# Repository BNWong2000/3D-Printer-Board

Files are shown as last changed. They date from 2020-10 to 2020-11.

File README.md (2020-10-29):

# 3D-Printer-Board
A custom, 3D printer controller, intended to run Klipper. All pcb source files were made in kiCAD. This project utilizes the stock kiCAD library for basic components (Resistors, Capacitors, Diodes, Inductors, Connectors, etc), and for the main chip (STM32F407IGT6). All other components were made as a custom library. 

#### Features:
* STM32F407IGT6 32 bit MCU
* 9 Silent Stepper Drivers (Trinamic TMC 2209 with UART control)
* 8 Fan output FETs
   * Selectable Voltage for each fan using jumpers. (24V, 12V or 5v)
* 8 Heater output FETs (including 1 high power FET for heated beds and 1 high power FET for heated chamber)
* High power step down converter to 5v (max 5A)
   * This is enough to power the raspberry pi (which only needs 3A at 5v) and several fans without an external power supply
* 12v step down converter for other peripherals.
* Fused inputs and outputs.

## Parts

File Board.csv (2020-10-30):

Reference | Value | Footprint | Datasheet
J1 | Conn_01x02 |  | ~
F1 | Keystone Fuse Holder |  | ~
C24 | 100nF |  | ~
C27 | 100nF |  | ~
F3 | Keystone Fuse Holder |  | ~
C26 | 100nF |  | ~
C29 | 100nF |  | ~
J2 | Conn_01x02 |  | ~
D1 | D_Schottky |  | ~
F2 | Keystone Fuse Holder |  | ~
C25 | 100nF |  | ~
C28 | 100nF |  | ~
U2 | A4403
U4 | AP7361C-33E-13
U3 | TPS54531
D2 | D_Schottky |  | ~
C31 | 4.7uF |  | ~
C32 | 100nF |  | ~
C30 | 4.7uF |  | ~
C43 | 0.01uF |  | ~
L2 | 4.7uH |  | ~
C44 | 100nF |  | ~
C49 | 47uF |  | ~
C51 | 47uF |  | ~
R10 | 10.2k |  | ~
R11 | 1.96k |  | ~
C47 | 47pF |  | ~
D5 | B540 |  | ~
C40 | 22pF |  | ~
C39 | 2200pF |  | ~
R6 | 37.4k |  | ~
F4 | 5A |  | ~
C42 | 10uF |  | ~
C46 | 10uF |  | ~
D3 | D_Schottky |  | ~
C37 | 10uF |  | ~
C38 | 100nF |  | ~
C36 | 100uF |  | ~
R7 | 200k |  | ~
JP3 | Jumper |  | ~
C41 | 100nF |  | ~
C45 | 22nF |  | ~
L3 | 10uH |  | ~
D4 | DB2W40300L |  | ~
R8 | 0.1 |  | ~
R9 | 0.1 |  | ~
R12 | 10.5k |  | ~
R13 | 750 |  | ~
C48 | 8.2nF |  | ~
C50 | 10uF |  | ~
C52 | 10uF |  | ~
C53 | 100nF |  | ~
JP22 | Jumper_3_Open |  | ~
D6 | LED |  | ~
R66 | 2.2k |  | ~
D7 | LED |  | ~
R67 | 2.2k |  | ~
D8 | LED |  | ~
R68 | 2.2k |  | ~
X_Driver1 | TMC2209
C63 | 100uF |  | ~
C65 | 10u |  | ~
C71 | 100nF |  | ~
C69 | 100nF |  | ~
C60 | 100nF |  | ~
C61 | 22nF |  | ~
C55 | 100nF |  | ~
C57 | 4.7uF |  | ~
R19 | 0R11 |  | ~
R21 | 0R11 |  | ~
C73 | 100nF |  | ~
C67 | 100nF |  | ~
R17 | 0R11 |  | ~
R15 | 20k |  | ~
JP5 | Stall Detection |  | ~
C75 | 1nF |  | ~
C77 | 1nF |  | ~
C79 | 1nF |  | ~
C81 | 1nF |  | ~
J4 | Conn_01x04 |  | ~
Y_Driver1 | TMC2209
C90 | 100uF |  | ~
C92 | 10u |  | ~
C98 | 100nF |  | ~
C96 | 100nF |  | ~
C86 | 100nF |  | ~
C87 | 22nF |  | ~
C82 | 100nF |  | ~
C84 | 4.7uF |  | ~
R26 | 0R11 |  | ~
R28 | 0R11 |  | ~
C100 | 100nF |  | ~
C94 | 100nF |  | ~
R24 | 0R11 |  | ~
R22 | 20k |  | ~
JP8 | Stall Detection |  | ~
C102 | 1nF |  | ~
C104 | 1nF |  | ~
C106 | 1nF |  | ~
C108 | 1nF |  | ~
J5 | Conn_01x04 |  | ~
Z_Driver1 | TMC2209
C62 | 100uF |  | ~
C64 | 10u |  | ~
C70 | 100nF |  | ~
C68 | 100nF |  | ~
C58 | 100nF |  | ~
C59 | 22nF |  | ~
C54 | 100nF |  | ~
C56 | 4.7uF |  | ~
R18 | 0R11 |  | ~
R20 | 0R11 |  | ~
C72 | 100nF |  | ~
C66 | 100nF |  | ~
R16 | 0R11 |  | ~
R14 | 20k |  | ~
JP4 | Stall Detection |  | ~
C74 | 1nF |  | ~
C76 | 1nF |  | ~
C78 | 1nF |  | ~
C80 | 1nF |  | ~
J3 | Conn_01x04 |  | ~
C91 | 100uF |  | ~
C93 | 10u |  | ~
C99 | 100nF |  | ~
C97 | 100nF |  | ~
C88 | 100nF |  | ~
C89 | 22nF |  | ~
C83 | 100nF |  | ~
C85 | 4.7uF |  | ~
R27 | 0R11 |  | ~
R29 | 0R11 |  | ~
C101 | 100nF |  | ~
C95 | 100nF |  | ~
R25 | 0R11 |  | ~
R23 | 20k |  | ~
JP9 | Stall Detection |  | ~
C103 | 1nF |  | ~
C105 | 1nF |  | ~
C107 | 1nF |  | ~
C109 | 1nF |  | ~
J6 | Conn_01x04 |  | ~
JP7 | SPREAD_STEALTH |  | ~
JP6 | SPREAD_STEALTH |  | ~
JP10 | SPREAD_STEALTH |  | ~
E0_Driver1 | TMC2209
JP11 | SPREAD_STEALTH |  | ~
U1 | STM32F407IGTx | Package_QFP:LQFP-176_24x24mm_P0.5mm | http://www.st.com/st-web-ui/static/active/en/resource/technical/document/datasheet/DM00037051.pdf
C2 | 100nF |  | ~
C4 | 4.7uF |  | ~
C6 | 100nF |  | ~
C7 | 100nF |  | ~
C8 | 100nF |  | ~
C9 | 100nF |  | ~
C10 | 100nF |  | ~
C11 | 100nF |  | ~
C12 | 100nF |  | ~
C13 | 100nF |  | ~
C14 | 100nF |  | ~
C5 | 100nF |  | ~
C15 | 100nF |  | ~
C16 | 100nF |  | ~
C17 | 100nF |  | ~
C18 | 100nF |  | ~
C19 | 4.7uF |  | ~
C3 | 2.2uF |  | ~
C1 | 2.2uF |  | ~
C20 | 100nF |  | ~
C21 | 1uF |  | ~
C22 | 1uF |  | ~
C23 | 100nF |  | ~
L1 | 10uH |  | ~
Y1 | 12MHz, 20pF |  | ~
C34 | 10pF |  | ~
C33 | 10pF |  | ~
R1 | 10k |  | ~
SW1 | SW_Push |  | ~
C35 | 100nF |  | ~
R2 | 1k |  | ~
R4 | 1k |  | ~
R3 | 10k |  | ~
R5 | 10k |  | ~
JP1 | Jumper_2_Open |  | ~
JP2 | Jumper_2_Open |  | ~
J12 | USB_B_Mini |  | ~
F5 | 500mA |  | ~
C182 | 0.1uF |  | ~
R69 | 22R |  | ~
R70 | 22R |  | ~
J13 | Micro_SD_Card |  | http://katalog.we-online.de/em/datasheet/693072010801.pdf
R72 | 10k |  | ~
R73 | 10k |  | ~
R71 | 10k |  | ~
R74 | 10k |  | ~
R75 | 10k |  | ~
C183 | 0.1uF |  | ~
EXP1 | Conn_02x05_Odd_Even |  | ~
EXP2 | Conn_02x05_Odd_Even |  | ~
UART1 | Conn_01x04 |  | ~
SPI1 | Conn_02x03_Odd_Even |  | ~
I2C1 | Conn_01x04 |  | ~
BLTouch1 | Conn_01x04 |  | ~
C187 | 100nF |  | ~
C184 | 100nF |  | ~
C185 | 100nF |  | ~
SWD1 | Conn_01x05 |  | ~
C186 | 100nF |  | ~
R78 | 10k |  | ~
R79 | 10k |  | ~
R80 | 10k |  | ~
U7 | 24C02
R76 | 10k |  | ~
R77 | 10k |  | ~
J55 | Conn_02x20_Odd_Even |  | ~
U5 | 74HCT245
C110 | 0.1uF |  | ~
R32 | 10k |  | ~
R30 | 10k |  | ~
R34 | 10k |  | ~
R36 | 10k |  | ~
R38 | 10k |  | ~
R40 | 10k |  | ~
R42 | 10k |  | ~
R44 | 10k |  | ~
U6 | 74HCT245
C111 | 0.1uF |  | ~
R33 | 10k |  | ~
R31 | 10k |  | ~
R35 | 10k |  | ~
R37 | 10k |  | ~
R39 | 10k |  | ~
R41 | 10k |  | ~
R43 | 10k |  | ~
R45 | 10k |  | ~
Q1 | Q_NMOS_GDS |  | ~
R81 | 100 |  | ~
D11 | Schottky |  | ~
D9 | LED |  | ~
R85 | 2.2k |  | ~
J16 | H0 |  | ~
Q5 | Q_NMOS_GDS |  | ~
R87 | 100 |  | ~
D17 | Schottky |  | ~
D15 | LED |  | ~
R91 | 2.2k |  | ~
J22 | H1 |  | ~
Q9 | Q_NMOS_GDS |  | ~
R93 | 100 |  | ~
D23 | Schottky |  | ~
D21 | LED |  | ~
R97 | 2.2k |  | ~
J28 | H2 |  | ~
Q13 | Q_NMOS_GDS |  | ~
R99 | 100 |  | ~
D29 | Schottky |  | ~
D27 | LED |  | ~
R103 | 2.2k |  | ~
J34 | H3 |  | ~
Q2 | Q_NMOS_GDS |  | ~
R82 | 100 |  | ~
D12 | Schottky |  | ~
D10 | LED |  | ~
R86 | 2.2k |  | ~
J17 | H4 |  | ~
Q6 | Q_NMOS_GDS |  | ~
R88 | 100 |  | ~
D18 | Schottky |  | ~
D16 | LED |  | ~
R92 | 2.2k |  | ~
J23 | H5 |  | ~
Q10 | Q_NMOS_GDS |  | ~
R94 | 100 |  | ~
D22 | LED |  | ~
R98 | 2.2k |  | ~
J29 | HC |  | ~
D24 | Schottky |  | ~
Q14 | Q_NMOS_GDS |  | ~
R100 | 100 |  | ~
D30 | Schottky |  | ~
D28 | LED |  | ~
R104 | 2.2k |  | ~
J35 | HB |  | ~
Q3 | Q_NMOS_GDS |  | ~
R83 | 100 |  | ~
D13 | Schottky |  | ~
J18 | F0 |  | ~
Q7 | Q_NMOS_GDS |  | ~
R89 | 100 |  | ~
D19 | Schottky |  | ~
J24 | F1 |  | ~
Q11 | Q_NMOS_GDS |  | ~
R95 | 100 |  | ~
D25 | Schottky |  | ~
J30 | F2 |  | ~
Q15 | Q_NMOS_GDS |  | ~
R101 | 100 |  | ~
D31 | Schottky |  | ~
J36 | F3 |  | ~
J14 | Conn_02x03_Odd_Even |  | ~
J20 | Conn_02x03_Odd_Even |  | ~
J26 | Conn_02x03_Odd_Even |  | ~
J32 | Conn_02x03_Odd_Even |  | ~
Q4 | Q_NMOS_GDS |  | ~
R84 | 100 |  | ~
D14 | Schottky |  | ~
J19 | F4 |  | ~
Q8 | Q_NMOS_GDS |  | ~
R90 | 100 |  | ~
D20 | Schottky |  | ~
J25 | F5 |  | ~
Q12 | Q_NMOS_GDS |  | ~
R96 | 100 |  | ~
D26 | Schottky |  | ~
J31 | F6 |  | ~
Q16 | Q_NMOS_GDS |  | ~
R102 | 100 |  | ~
D32 | Schottky |  | ~
J37 | F7 |  | ~
J15 | Conn_02x03_Odd_Even |  | ~
J21 | Conn_02x03_Odd_Even |  | ~
J27 | Conn_02x03_Odd_Even |  | ~
J33 | Conn_02x03_Odd_Even |  | ~
J42 | Conn_01x03 |  | ~
D42 | LED |  | ~
C192 | 2.2uF |  | ~
R111 | 10k |  | ~
R114 | 2.2k |  | ~
J38 | Conn_01x03 |  | ~
D35 | LED |  | ~
C188 | 2.2uF |  | ~
R105 | 10k |  | ~
R107 | 2.2k |  | ~
J44 | Conn_01x03 |  | ~
D46 | LED |  | ~
C194 | 2.2uF |  | ~
R116 | 10k |  | ~
R118 | 2.2k |  | ~
J46 | Conn_01x03 |  | ~
D50 | LED |  | ~
C196 | 2.2uF |  | ~
R120 | 10k |  | ~
R122 | 2.2k |  | ~
J39 | Conn_01x03 |  | ~
D36 | LED |  | ~
C189 | 2.2uF |  | ~
R106 | 10k |  | ~
R108 | 2.2k |  | ~
J40 | Conn_01x03 |  | ~
D40 | LED |  | ~
C190 | 2.2uF |  | ~
R109 | 10k |  | ~
R112 | 2.2k |  | ~
J43 | Conn_01x03 |  | ~
D45 | LED |  | ~
C193 | 2.2uF |  | ~
R115 | 10k |  | ~
R117 | 2.2k |  | ~
J45 | Conn_01x03 |  | ~
D49 | LED |  | ~
C195 | 2.2uF |  | ~
R119 | 10k |  | ~
R121 | 2.2k |  | ~
J41 | Conn_01x03 |  | ~
D41 | LED |  | ~
C191 | 2.2uF |  | ~
R110 | 10k |  | ~
R113 | 2.2k |  | ~
D33 | Schottky |  | ~
D39 | Schottky |  | ~
D44 | Schottky |  | ~
D48 | Schottky |  | ~
D47 | Schottky |  | ~
D43 | Schottky |  | ~
D37 | Schottky |  | ~
D34 | Schottky |  | ~
D38 | Schottky |  | ~
J47 | Conn_01x02 |  | ~
R123 | 4.7k |  | ~
C197 | 2.2uF |  | ~
D51 | S_D |  | ~
D52 | S_D |  | ~
J49 | Conn_01x02 |  | ~
R125 | 4.7k |  | ~
C199 | 2.2uF |  | ~
D55 | S_D |  | ~
D56 | S_D |  | ~
J51 | Conn_01x02 |  | ~
R127 | 4.7k |  | ~
C201 | 2.2uF |  | ~
D59 | S_D |  | ~
D60 | S_D |  | ~
J53 | Conn_01x02 |  | ~
R129 | 4.7k |  | ~
C203 | 2.2uF |  | ~
D63 | S_D |  | ~
D64 | S_D |  | ~
J48 | Conn_01x02 |  | ~
R124 | 4.7k |  | ~
C198 | 2.2uF |  | ~
D53 | S_D |  | ~
D54 | S_D |  | ~
J50 | Conn_01x02 |  | ~
R126 | 4.7k |  | ~
C200 | 2.2uF |  | ~
D57 | S_D |  | ~
D58 | S_D |  | ~
J52 | Conn_01x02 |  | ~
R128 | 4.7k |  | ~
C202 | 2.2uF |  | ~
D61 | S_D |  | ~
D62 | S_D |  | ~
J54 | Conn_01x02 |  | ~
R130 | 4.7k |  | ~
C204 | 2.2uF |  | ~
D65 | S_D |  | ~
D66 | S_D |  | ~
E1_Driver1 | TMC2209
C121 | 100uF |  | ~
C123 | 10u |  | ~
C129 | 100nF |  | ~
C127 | 100nF |  | ~
C118 | 100nF |  | ~
C119 | 22nF |  | ~
C113 | 100nF |  | ~
C115 | 4.7uF |  | ~
R51 | 0R11 |  | ~
R53 | 0R11 |  | ~
C131 | 100nF |  | ~
C125 | 100nF |  | ~
R49 | 0R11 |  | ~
R47 | 20k |  | ~
JP13 | Stall Detection |  | ~
C133 | 1nF |  | ~
C135 | 1nF |  | ~
C137 | 1nF |  | ~
C139 | 1nF |  | ~
J8 | Conn_01x04 |  | ~
E2_Driver1 | TMC2209
C148 | 100uF |  | ~
C150 | 10u |  | ~
C156 | 100nF |  | ~
C154 | 100nF |  | ~
C144 | 100nF |  | ~
C145 | 22nF |  | ~
C140 | 100nF |  | ~
C142 | 4.7uF |  | ~
R58 | 0R11 |  | ~
R60 | 0R11 |  | ~
C158 | 100nF |  | ~
C152 | 100nF |  | ~
R56 | 0R11 |  | ~
R54 | 20k |  | ~
JP16 | Stall Detection |  | ~
C160 | 1nF |  | ~
C162 | 1nF |  | ~
C164 | 1nF |  | ~
C166 | 1nF |  | ~
J9 | Conn_01x04 |  | ~
E3_Driver1 | TMC2209
C120 | 100uF |  | ~
C122 | 10u |  | ~
C128 | 100nF |  | ~
C126 | 100nF |  | ~
C116 | 100nF |  | ~
C117 | 22nF |  | ~
C112 | 100nF |  | ~
C114 | 4.7uF |  | ~
R50 | 0R11 |  | ~
R52 | 0R11 |  | ~
C130 | 100nF |  | ~
C124 | 100nF |  | ~
R48 | 0R11 |  | ~
R46 | 20k |  | ~
JP12 | Stall Detection |  | ~
C132 | 1nF |  | ~
C134 | 1nF |  | ~
C136 | 1nF |  | ~
C138 | 1nF |  | ~
J7 | Conn_01x04 |  | ~
C149 | 100uF |  | ~
C151 | 10u |  | ~
C157 | 100nF |  | ~
C155 | 100nF |  | ~
C146 | 100nF |  | ~
C147 | 22nF |  | ~
C141 | 100nF |  | ~
C143 | 4.7uF |  | ~
R59 | 0R11 |  | ~
R61 | 0R11 |  | ~
C159 | 100nF |  | ~
C153 | 100nF |  | ~
R57 | 0R11 |  | ~
R55 | 20k |  | ~
JP17 | Stall Detection |  | ~
C161 | 1nF |  | ~
C163 | 1nF |  | ~
C165 | 1nF |  | ~
C167 | 1nF |  | ~
J10 | Conn_01x04 |  | ~
JP15 | SPREAD_STEALTH |  | ~
JP14 | SPREAD_STEALTH |  | ~
JP18 | SPREAD_STEALTH |  | ~
E4_Driver1 | TMC2209
JP19 | SPREAD_STEALTH |  | ~
C172 | 100uF |  | ~
C173 | 10u |  | ~
C176 | 100nF |  | ~
C175 | 100nF |  | ~
C170 | 100nF |  | ~
C171 | 22nF |  | ~
C168 | 100nF |  | ~
C169 | 4.7uF |  | ~
R64 | 0R11 |  | ~
R65 | 0R11 |  | ~
C177 | 100nF |  | ~
C174 | 100nF |  | ~
R63 | 0R11 |  | ~
R62 | 20k |  | ~
JP20 | Stall Detection |  | ~
C178 | 1nF |  | ~
C179 | 1nF |  | ~
C180 | 1nF |  | ~
C181 | 1nF |  | ~
J11 | Conn_01x04 |  | ~
E5_Driver1 | TMC2209
JP21 | SPREAD_STEALTH |  | ~

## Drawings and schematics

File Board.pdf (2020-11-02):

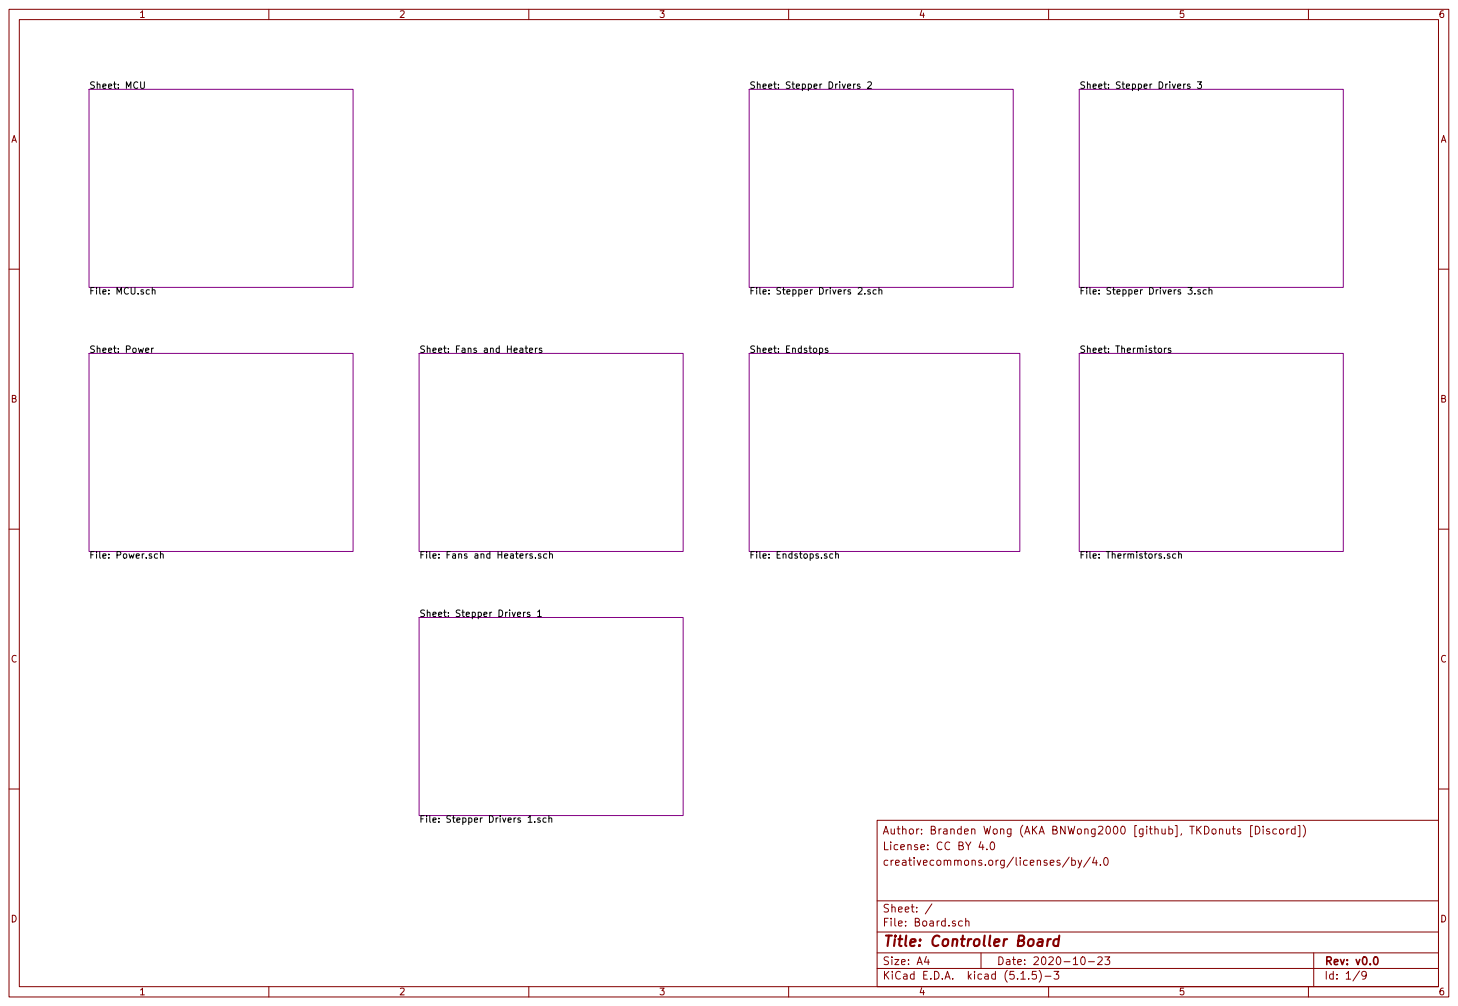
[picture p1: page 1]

File: Stepper Drivers 2.sch

File: Stepper Drivers 3.sch

File: Stepper Drivers 1.sch

License: CC BY 4.0 Author: Branden Wong (AKA BNWong2000 [github], TKDonuts [Discord])

File: Board.sch Sheet: / creativecommons.org/licenses/by/4.0

Id: 1/9 Title: Controller Board

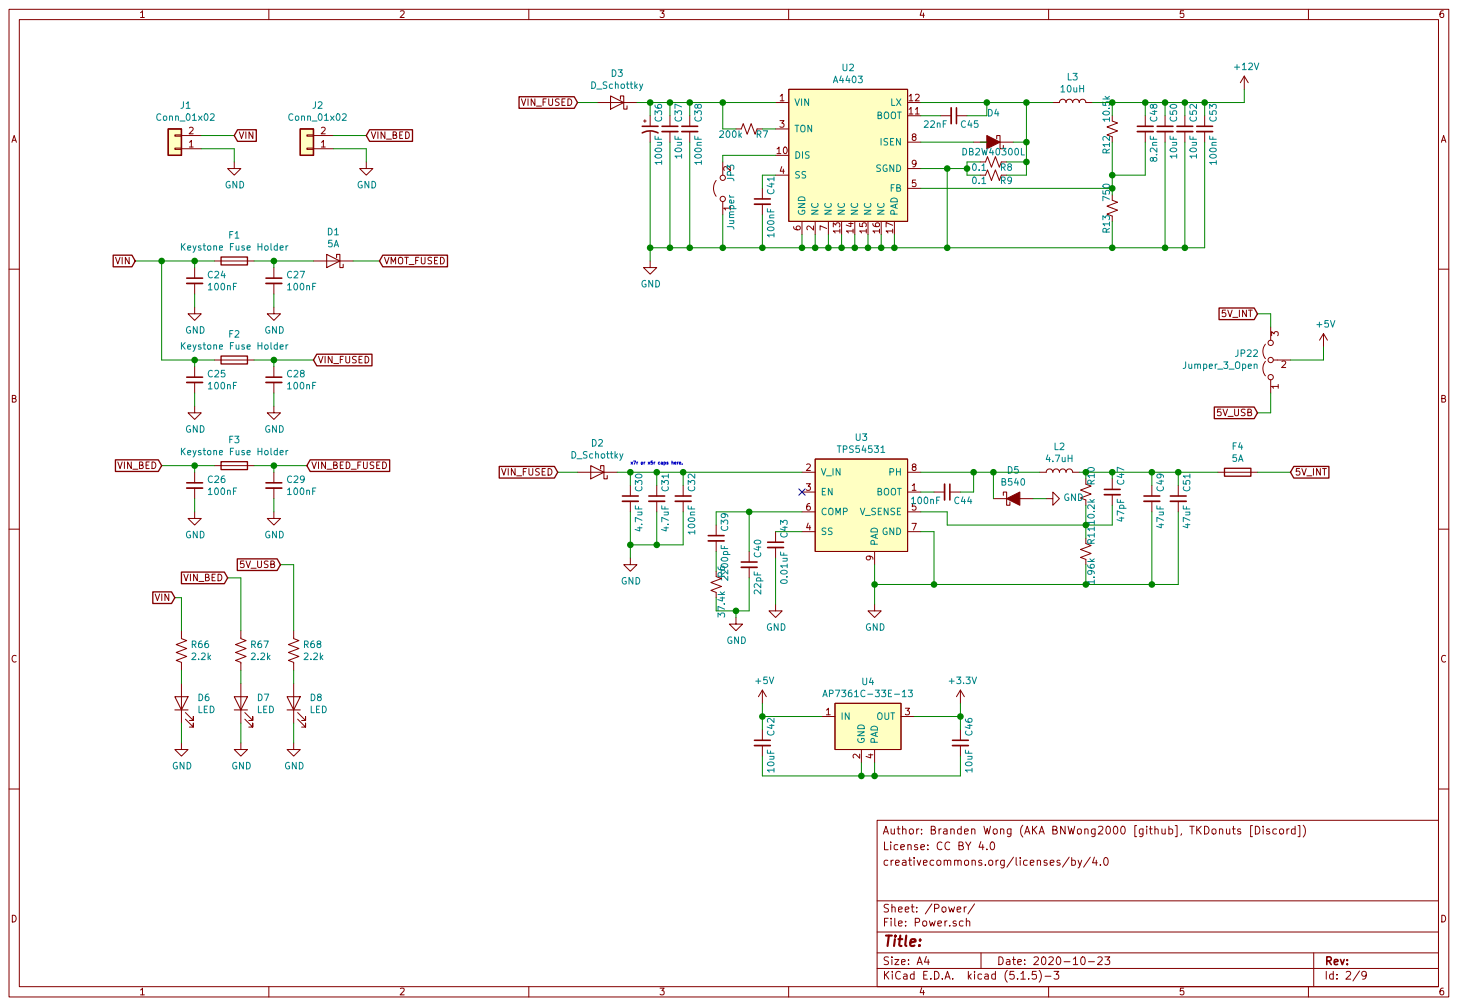
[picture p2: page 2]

2 TON 3 SS 4 FB 5 GND

License: CC BY 4.0 Author: Branden Wong (AKA BNWong2000 [github], TKDonuts [Discord])

Id: 2/9 Title: File: Power.sch Sheet: /Power/ creativecommons.org/licenses/by/4.0

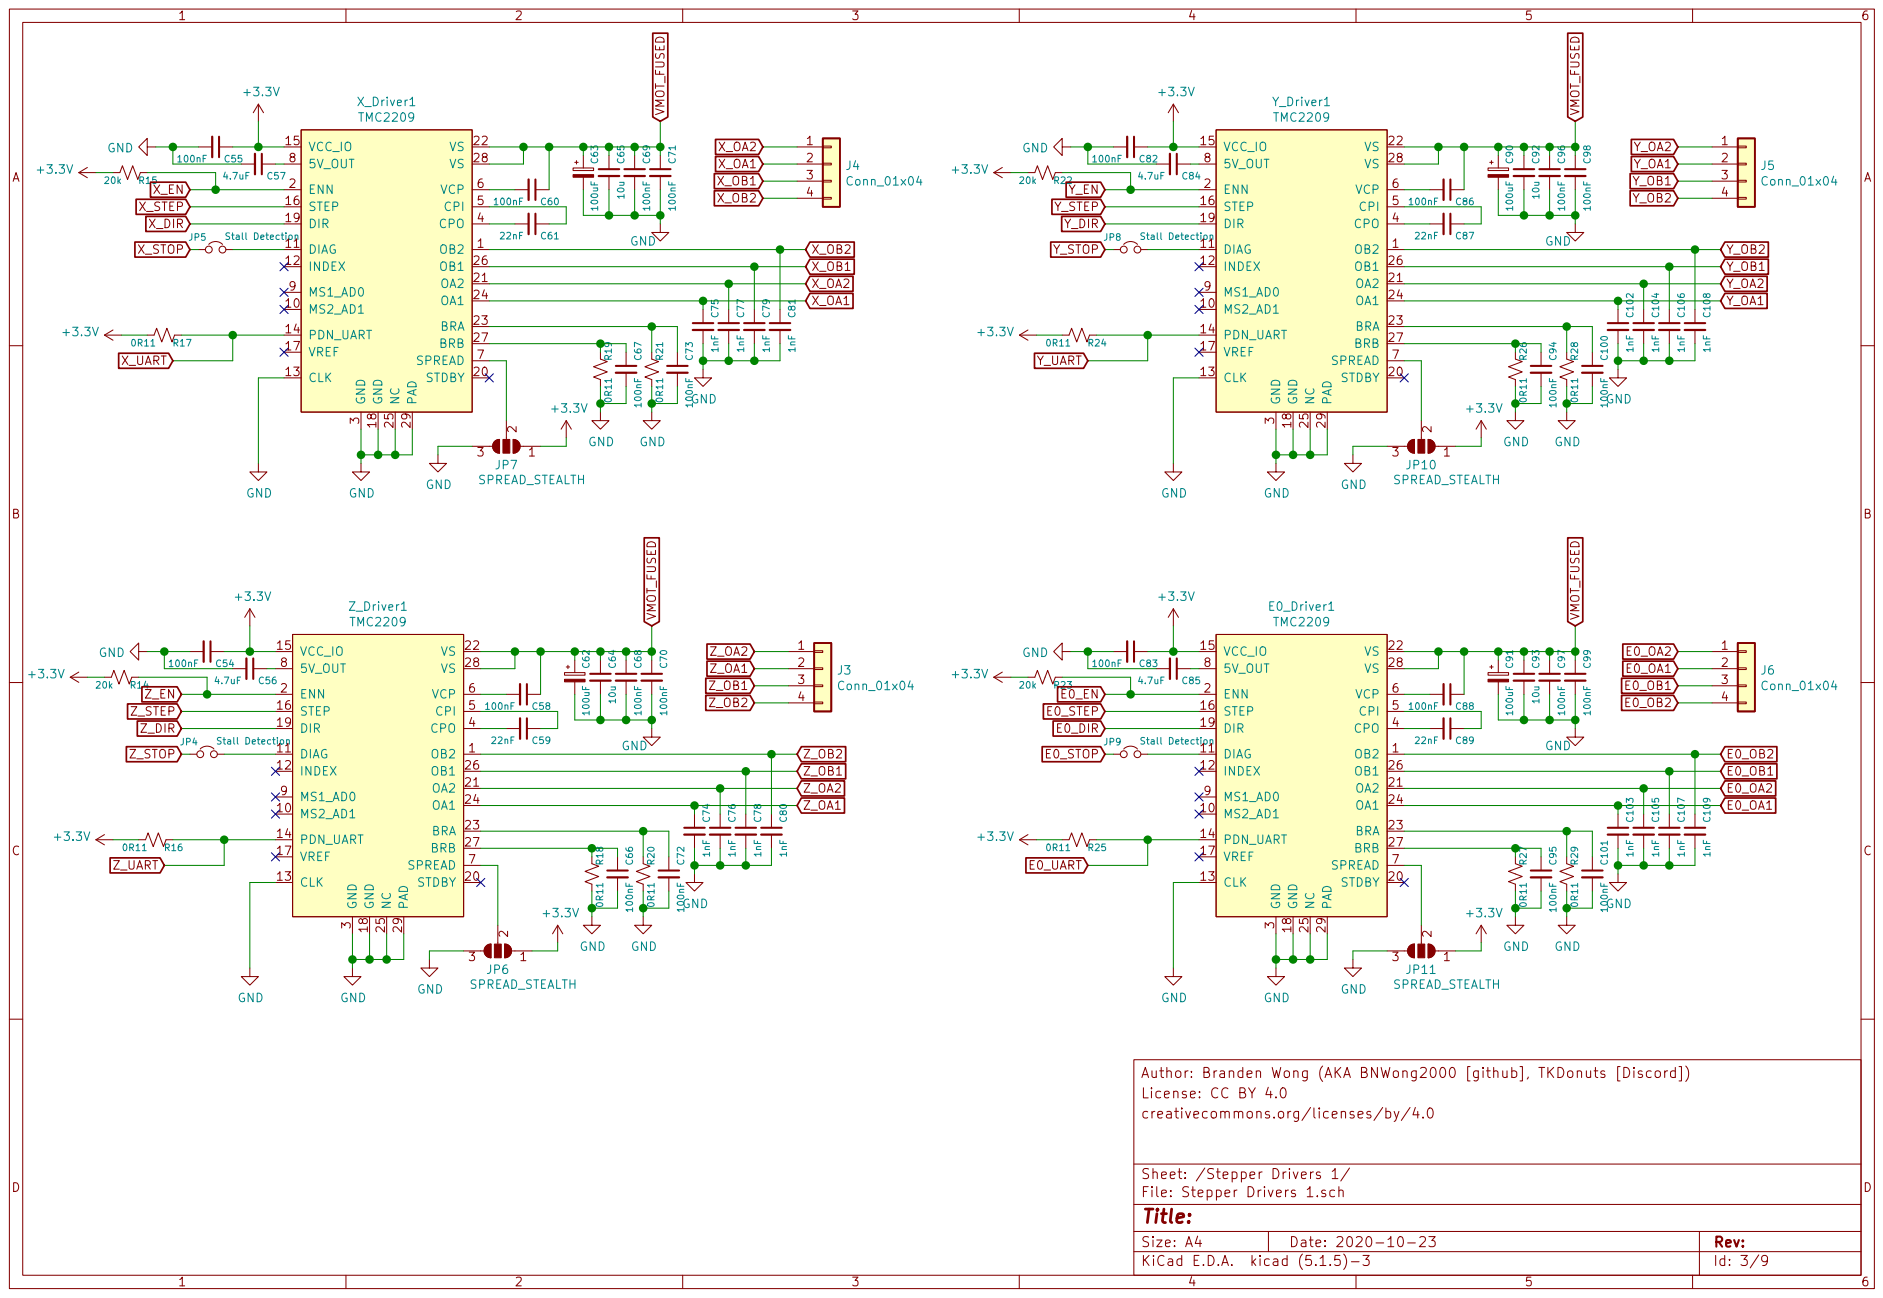
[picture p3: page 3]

3 CPO 4 CPI 5 VCP 6 SPREAD 7

License: CC BY 4.0 Author: Branden Wong (AKA BNWong2000 [github], TKDonuts [Discord]) C70 100nF

creativecommons.org/licenses/by/4.0

Sheet: /Stepper Drivers 1/
File: Stepper Drivers 1.sch
Id: 3/9 Title:

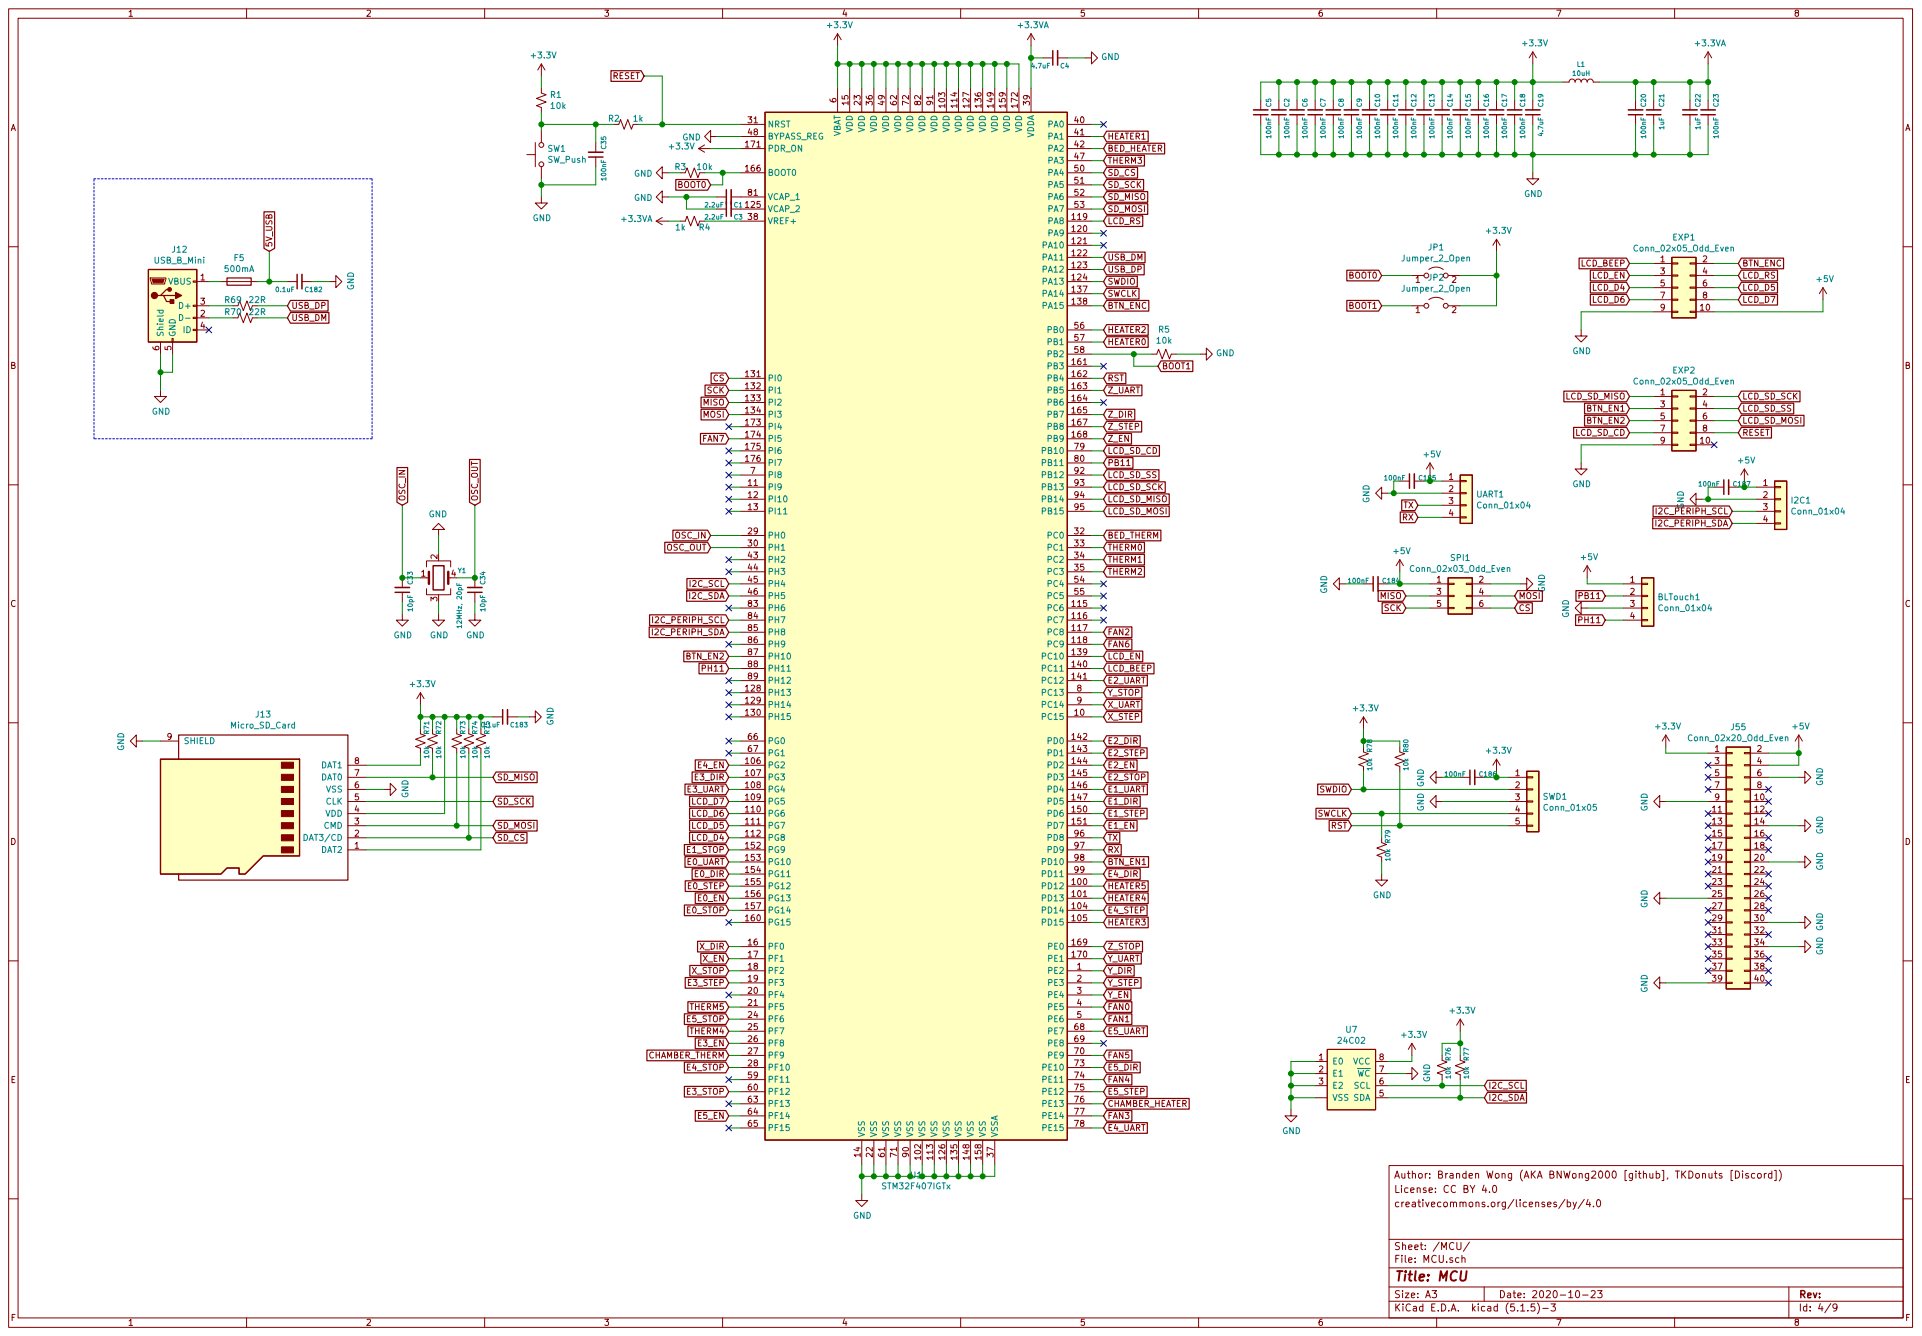
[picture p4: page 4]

License: CC BY 4.0 Author: Branden Wong (AKA BNWong2000 [github], TKDonuts [Discord])

File: MCU.sch Sheet: /MCU/ creativecommons.org/licenses/by/4.0

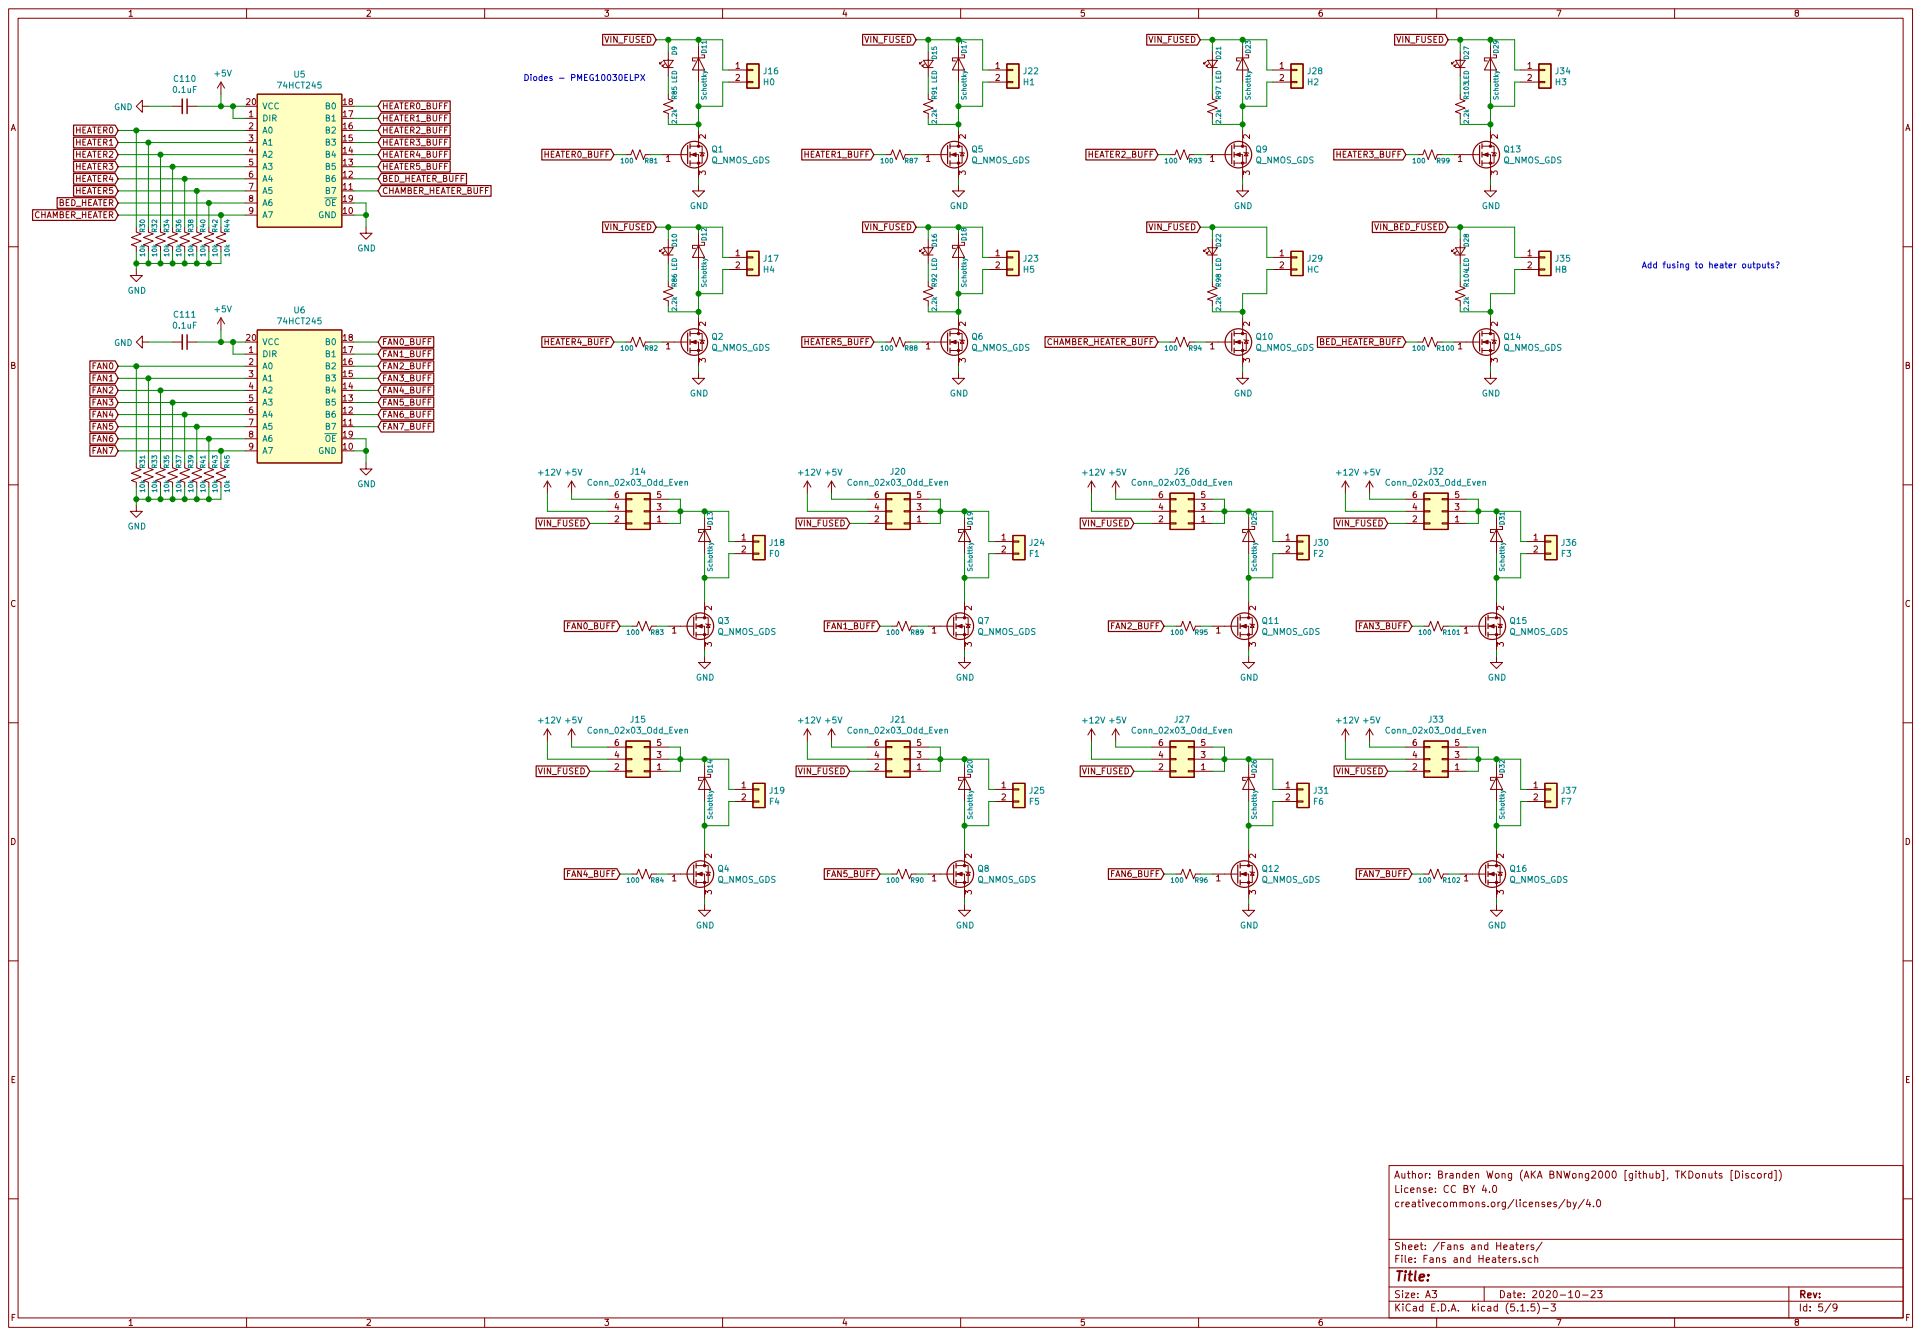
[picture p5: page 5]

2 3 Q4 Q_NMOS_GDS R30 10k DIR 1 GND 10 B7 11 B6 12 B5 13 B4 14 B3 15 B2 16 B1 17 B0 18 OE 19 A0 2 VCC 20 A1 3 A2 4 A3 5 A4 6 A5 7 A6 8 A7 9 U6

Add fusing to heater outputs?

Id: 5/9 Title: File: Fans and Heaters.sch Sheet: /Fans and Heaters/ creativecommons.org/licenses/by/4.0

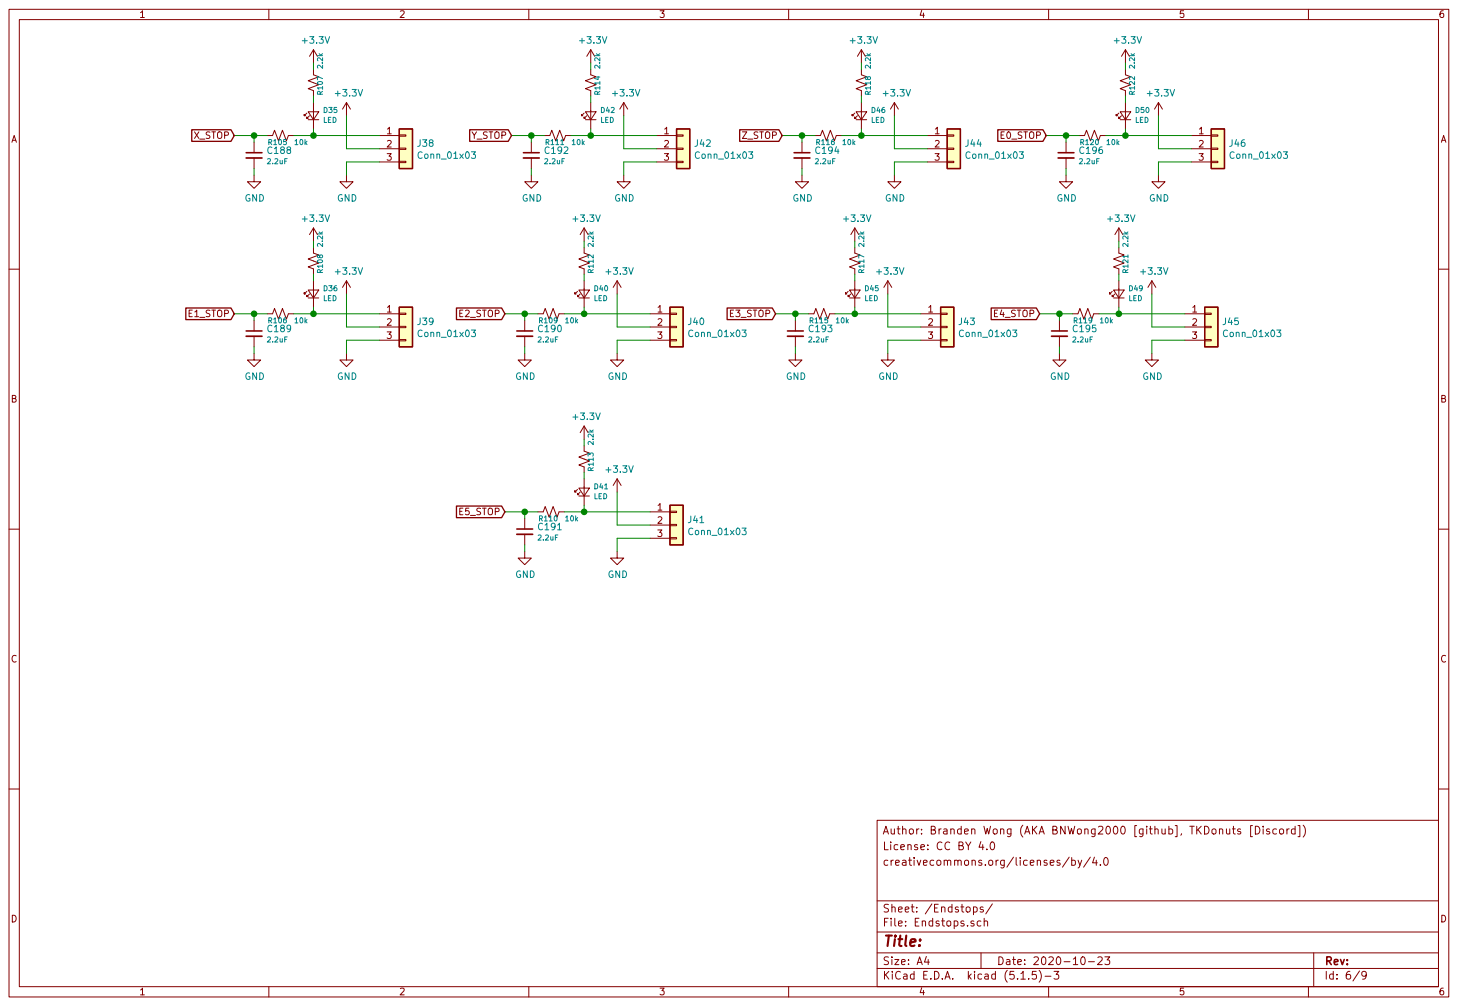
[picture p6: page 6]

License: CC BY 4.0 Author: Branden Wong (AKA BNWong2000 [github], TKDonuts [Discord])

creativecommons.org/licenses/by/4.0

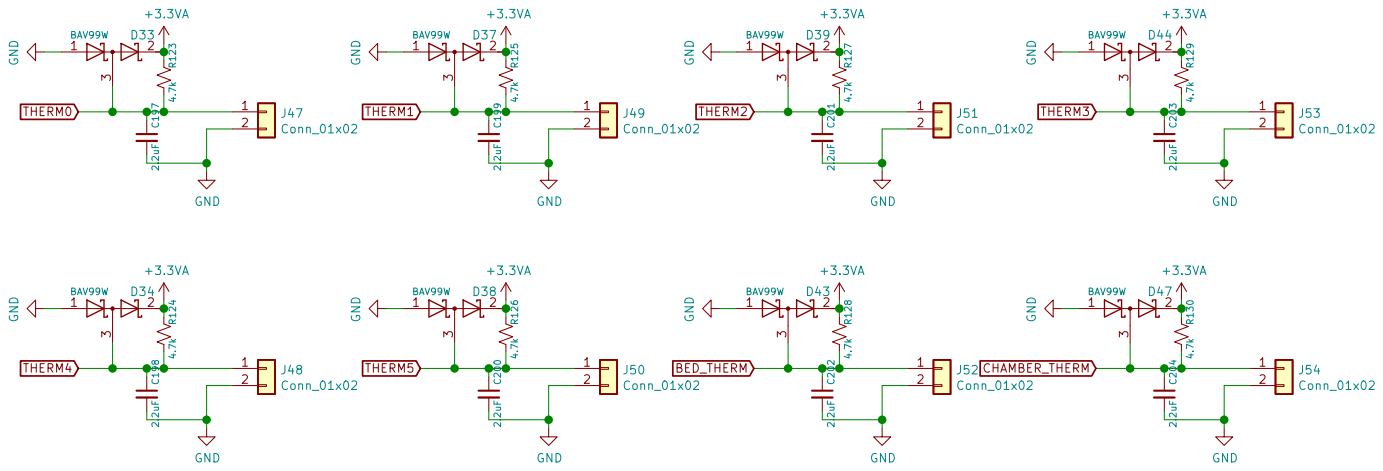
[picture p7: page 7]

License: CC BY 4.0 Author: Branden Wong (AKA BNWong2000 [github], TKDonuts [Discord]) GND GND

Id: 7/9 Title: File: Thermistors.sch Sheet: /Thermistors/ creativecommons.org/licenses/by/4.0

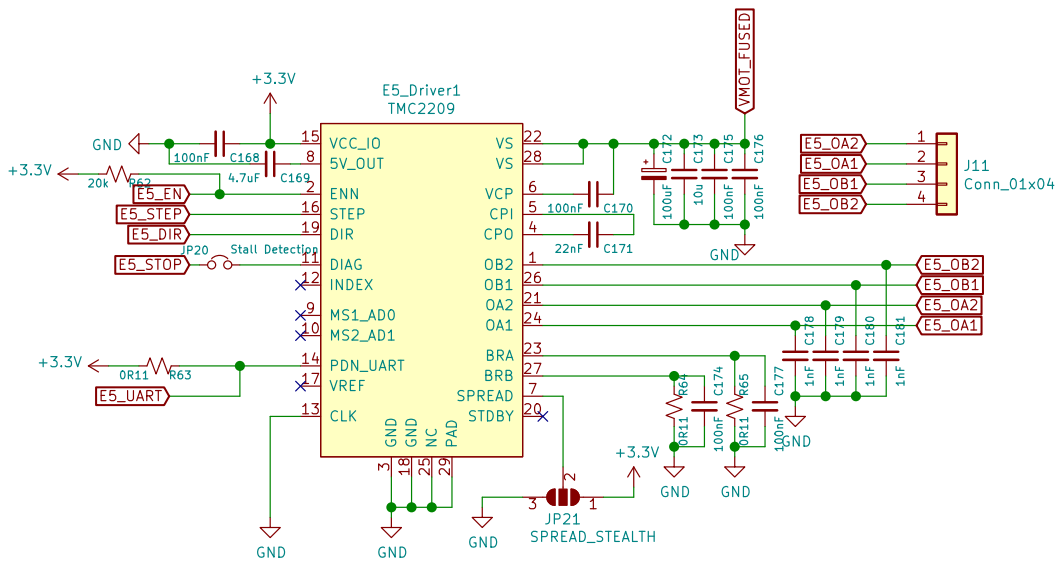
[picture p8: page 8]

3 CPO 4 CPI 5 VCP 6 SPREAD 7

Sheet: /Stepper Drivers 3/
File: Stepper Drivers 3.sch
Id: 8/9 Title:

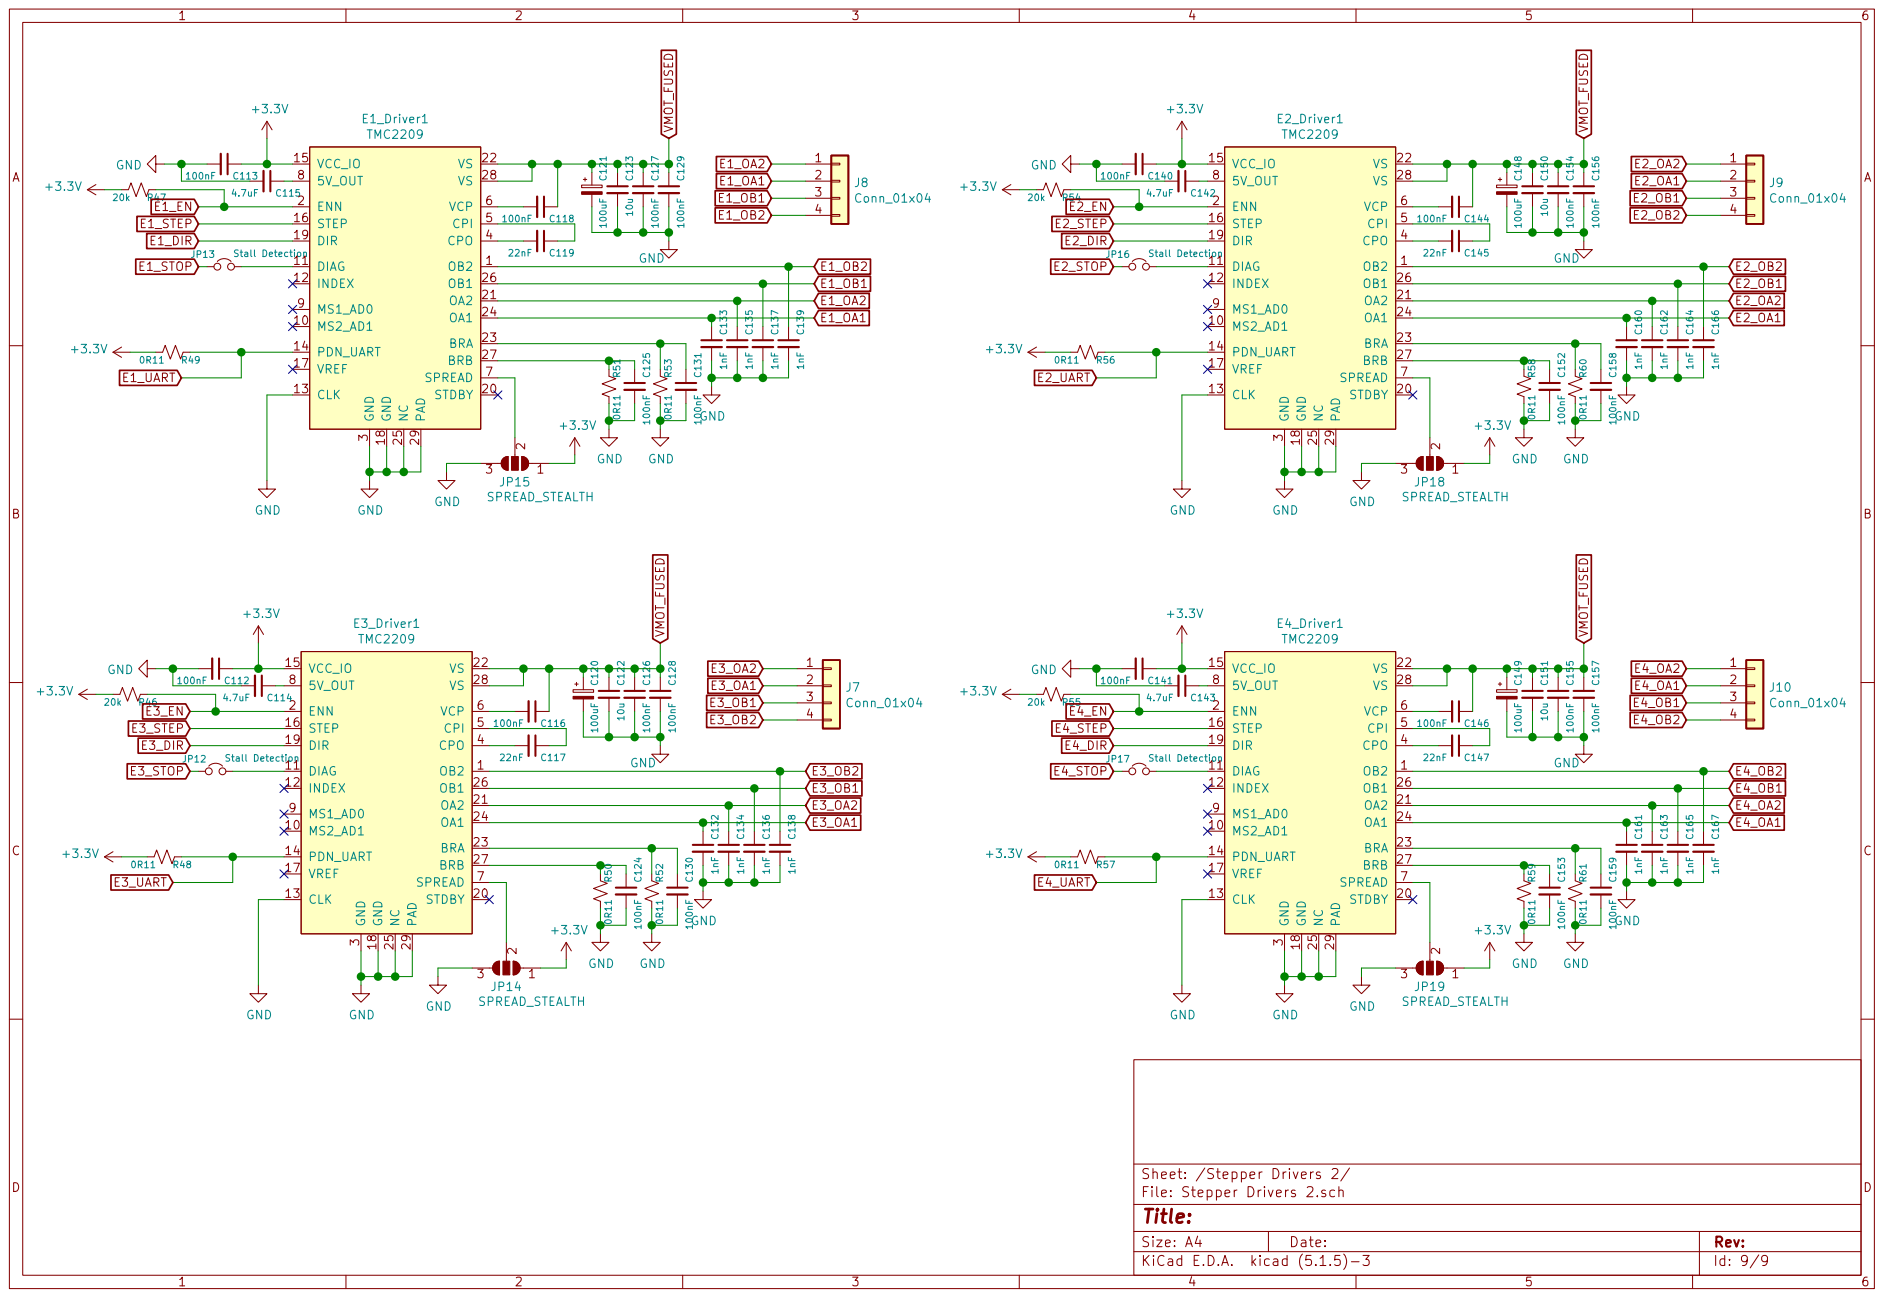
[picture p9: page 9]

3 CPO 4 CPI 5 VCP 6 SPREAD 7

Sheet: /Stepper Drivers 2/
File: Stepper Drivers 2.sch
Id: 9/9 Title:

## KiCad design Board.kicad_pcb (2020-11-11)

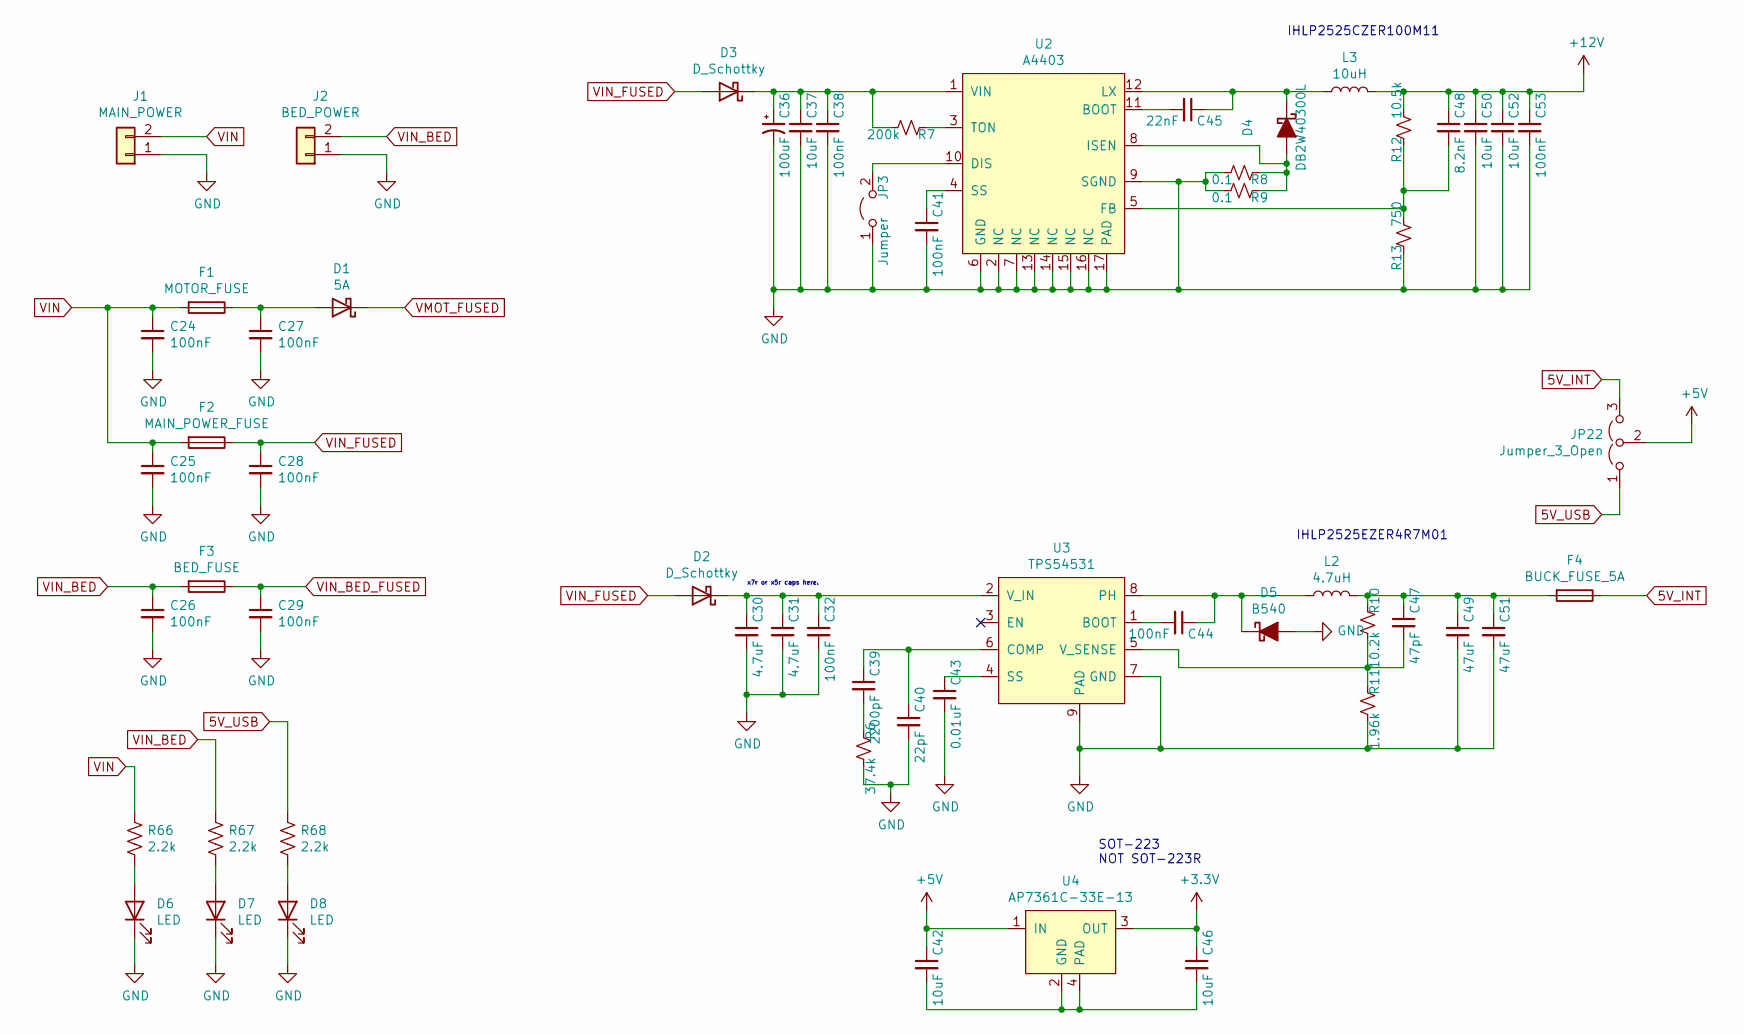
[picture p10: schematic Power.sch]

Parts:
C24, C25, C26, C27, C28, C29, C32, C38, C41, C44, C53: 100nF; C_0603_1608Metric_Pad1.05x0.95mm_HandSolder
C30, C31: 4.7uF; C_0805_2012Metric_Pad1.15x1.40mm_HandSolder
C36: 100uF; CP_Elec_6.3x7.7
C37, C42, C46, C50, C52: 10uF; C_0805_2012Metric_Pad1.15x1.40mm_HandSolder
C39: 2200pF; C_0603_1608Metric_Pad1.05x0.95mm_HandSolder
C40: 22pF; C_0603_1608Metric_Pad1.05x0.95mm_HandSolder
C43: 0.01uF; C_0603_1608Metric_Pad1.05x0.95mm_HandSolder
C45: 22nF; C_0603_1608Metric_Pad1.05x0.95mm_HandSolder
C47: 47pF; C_0603_1608Metric_Pad1.05x0.95mm_HandSolder
C48: 8.2nF; C_0603_1608Metric_Pad1.05x0.95mm_HandSolder
C49, C51: 47uF; C_0603_1608Metric_Pad1.05x0.95mm_HandSolder
D1: 5A; D_SMA_Handsoldering
D2, D3: D_Schottky; D_SOD-123F
D4: DB2W40300L; D_SOD-123F
D5: B540; D_SMC_Handsoldering
D6, D7, D8: LED; LED_0603_1608Metric_Pad1.05x0.95mm_HandSolder
F1: MOTOR_FUSE; Fuseholder_Blade_Mini_Keystone_3568
F2: MAIN_POWER_FUSE; Fuseholder_Blade_Mini_Keystone_3568
F3: BED_FUSE; Fuseholder_Blade_Mini_Keystone_3568
F4: BUCK_FUSE_5A; Fuseholder_Blade_Mini_Keystone_3568
J1: MAIN_POWER; TerminalBlock_Dinkle_DT-55-B01X-02_P10.00mm
J2: BED_POWER; TerminalBlock_Dinkle_DT-55-B01X-02_P10.00mm
JP3: Jumper; PinHeader_1x02_P2.54mm_Vertical
JP22: Jumper_3_Open; PinHeader_1x03_P2.54mm_Vertical
L2: 4.7uH; L_Vishay_IHLP-2525
L3: 10uH; L_Vishay_IHLP-2525
R6: 37.4k; R_0603_1608Metric_Pad1.05x0.95mm_HandSolder
R7: 200k; R_0603_1608Metric_Pad1.05x0.95mm_HandSolder
R8, R9: 0.1; R_1206_3216Metric_Pad1.42x1.75mm_HandSolder
R10: 10.2k; R_0603_1608Metric_Pad1.05x0.95mm_HandSolder
R11: 1.96k; R_0603_1608Metric_Pad1.05x0.95mm_HandSolder
R12: 10.5k; R_0603_1608Metric_Pad1.05x0.95mm_HandSolder
R13: 750; R_0603_1608Metric_Pad1.05x0.95mm_HandSolder
R66, R67, R68: 2.2k; R_0603_1608Metric_Pad1.05x0.95mm_HandSolder
U2: A4403; QFN-16-1EP_4x4mm_P0.65mm_EP2.7x2.7mm_ThermalVias
U3: TPS54531; TI_SO-PowerPAD-8_ThermalVias
U4: AP7361C-33E-13; SOT-223

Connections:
5V_INT: F4.1, JP22.3 (B)
5V_USB: JP22.1 (A), R68.1; also elsewhere on the board
+3V3: C46.1, U4.3 (OUT); also elsewhere on the board
+5V: C42.1, JP22.2 (C), U4.1 (IN); also elsewhere on the board
+12V: C48.1, C50.1, C52.1, C53.1, L3.2, R12.2; also elsewhere on the board
GND: C24.2, C25.2, C26.2, C27.2, C28.2, C29.2, C30.2, C31.2, C32.2, C36.2, C37.2, C38.2, C40.2, C41.2, C43.2, C49.2, C50.2, C51.2, C52.2, C53.2, D5.2 (A), D6.1 (K), D7.1 (K), D8.1 (K), J1.1, J2.1, JP3.1 (A), R6.2, R8.2, R9.2, R11.2, R13.1, U2.2 (NC), U2.6 (GND), U2.7 (NC), U2.9 (SGND), U2.13 (NC), U2.14 (NC), U2.15 (NC), U2.16 (NC), U2.17 (PAD), U3.7 (GND), U3.9 (PAD); also elsewhere on the board
unnamed: C27.1, D1.2 (A), F1.1
unnamed: C30.1, C31.1, C32.1, D2.1 (K), U3.2 (V_IN)
unnamed: C36.1, C37.1, C38.1, D3.1 (K), R7.2, U2.1 (VIN)
unnamed: C39.1, C40.1, U3.6 (COMP)
unnamed: C39.2, R6.1
unnamed: C41.1, U2.4 (SS)
unnamed: C42.2, C46.2, U4.2 (GND), U4.4 (PAD)
unnamed: C43.1, U3.4 (SS)
unnamed: C44.1, D5.1 (K), L2.1, U3.8 (PH)
unnamed: C44.2, U3.1 (BOOT)
unnamed: C45.1, D4.1 (K), L3.1, U2.12 (LX)
unnamed: C45.2, U2.11 (BOOT)
unnamed: C47.1, C49.1, C51.1, F4.2, L2.2, R10.1
unnamed: C47.2, R10.2, R11.1, U3.5 (V_SENSE)
unnamed: C48.2, R12.1, R13.2, U2.5 (FB)
unnamed: D4.2 (A), R8.1, R9.1, U2.8 (ISEN)
unnamed: D6.2 (A), R66.2
unnamed: D7.2 (A), R67.2
unnamed: D8.2 (A), R68.2
unnamed: JP3.2 (B), U2.10 (DIS)
unnamed: R7.1, U2.3 (TON)
VIN: C24.1, C25.1, F1.2, F2.2, J1.2, R66.1
VIN_BED: C26.1, F3.2, J2.2, R67.1
VIN_BED_FUSED: C29.1, F3.1; also elsewhere on the board
VIN_FUSED: C28.1, D2.2 (A), D3.2 (A), F2.1; also elsewhere on the board
VMOT_FUSED: D1.1 (K); also elsewhere on the board

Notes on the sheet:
x7r or x5r caps here.
IHLP2525CZER100M11
IHLP2525EZER4R7M01
SOT-223 NOT SOT-223R

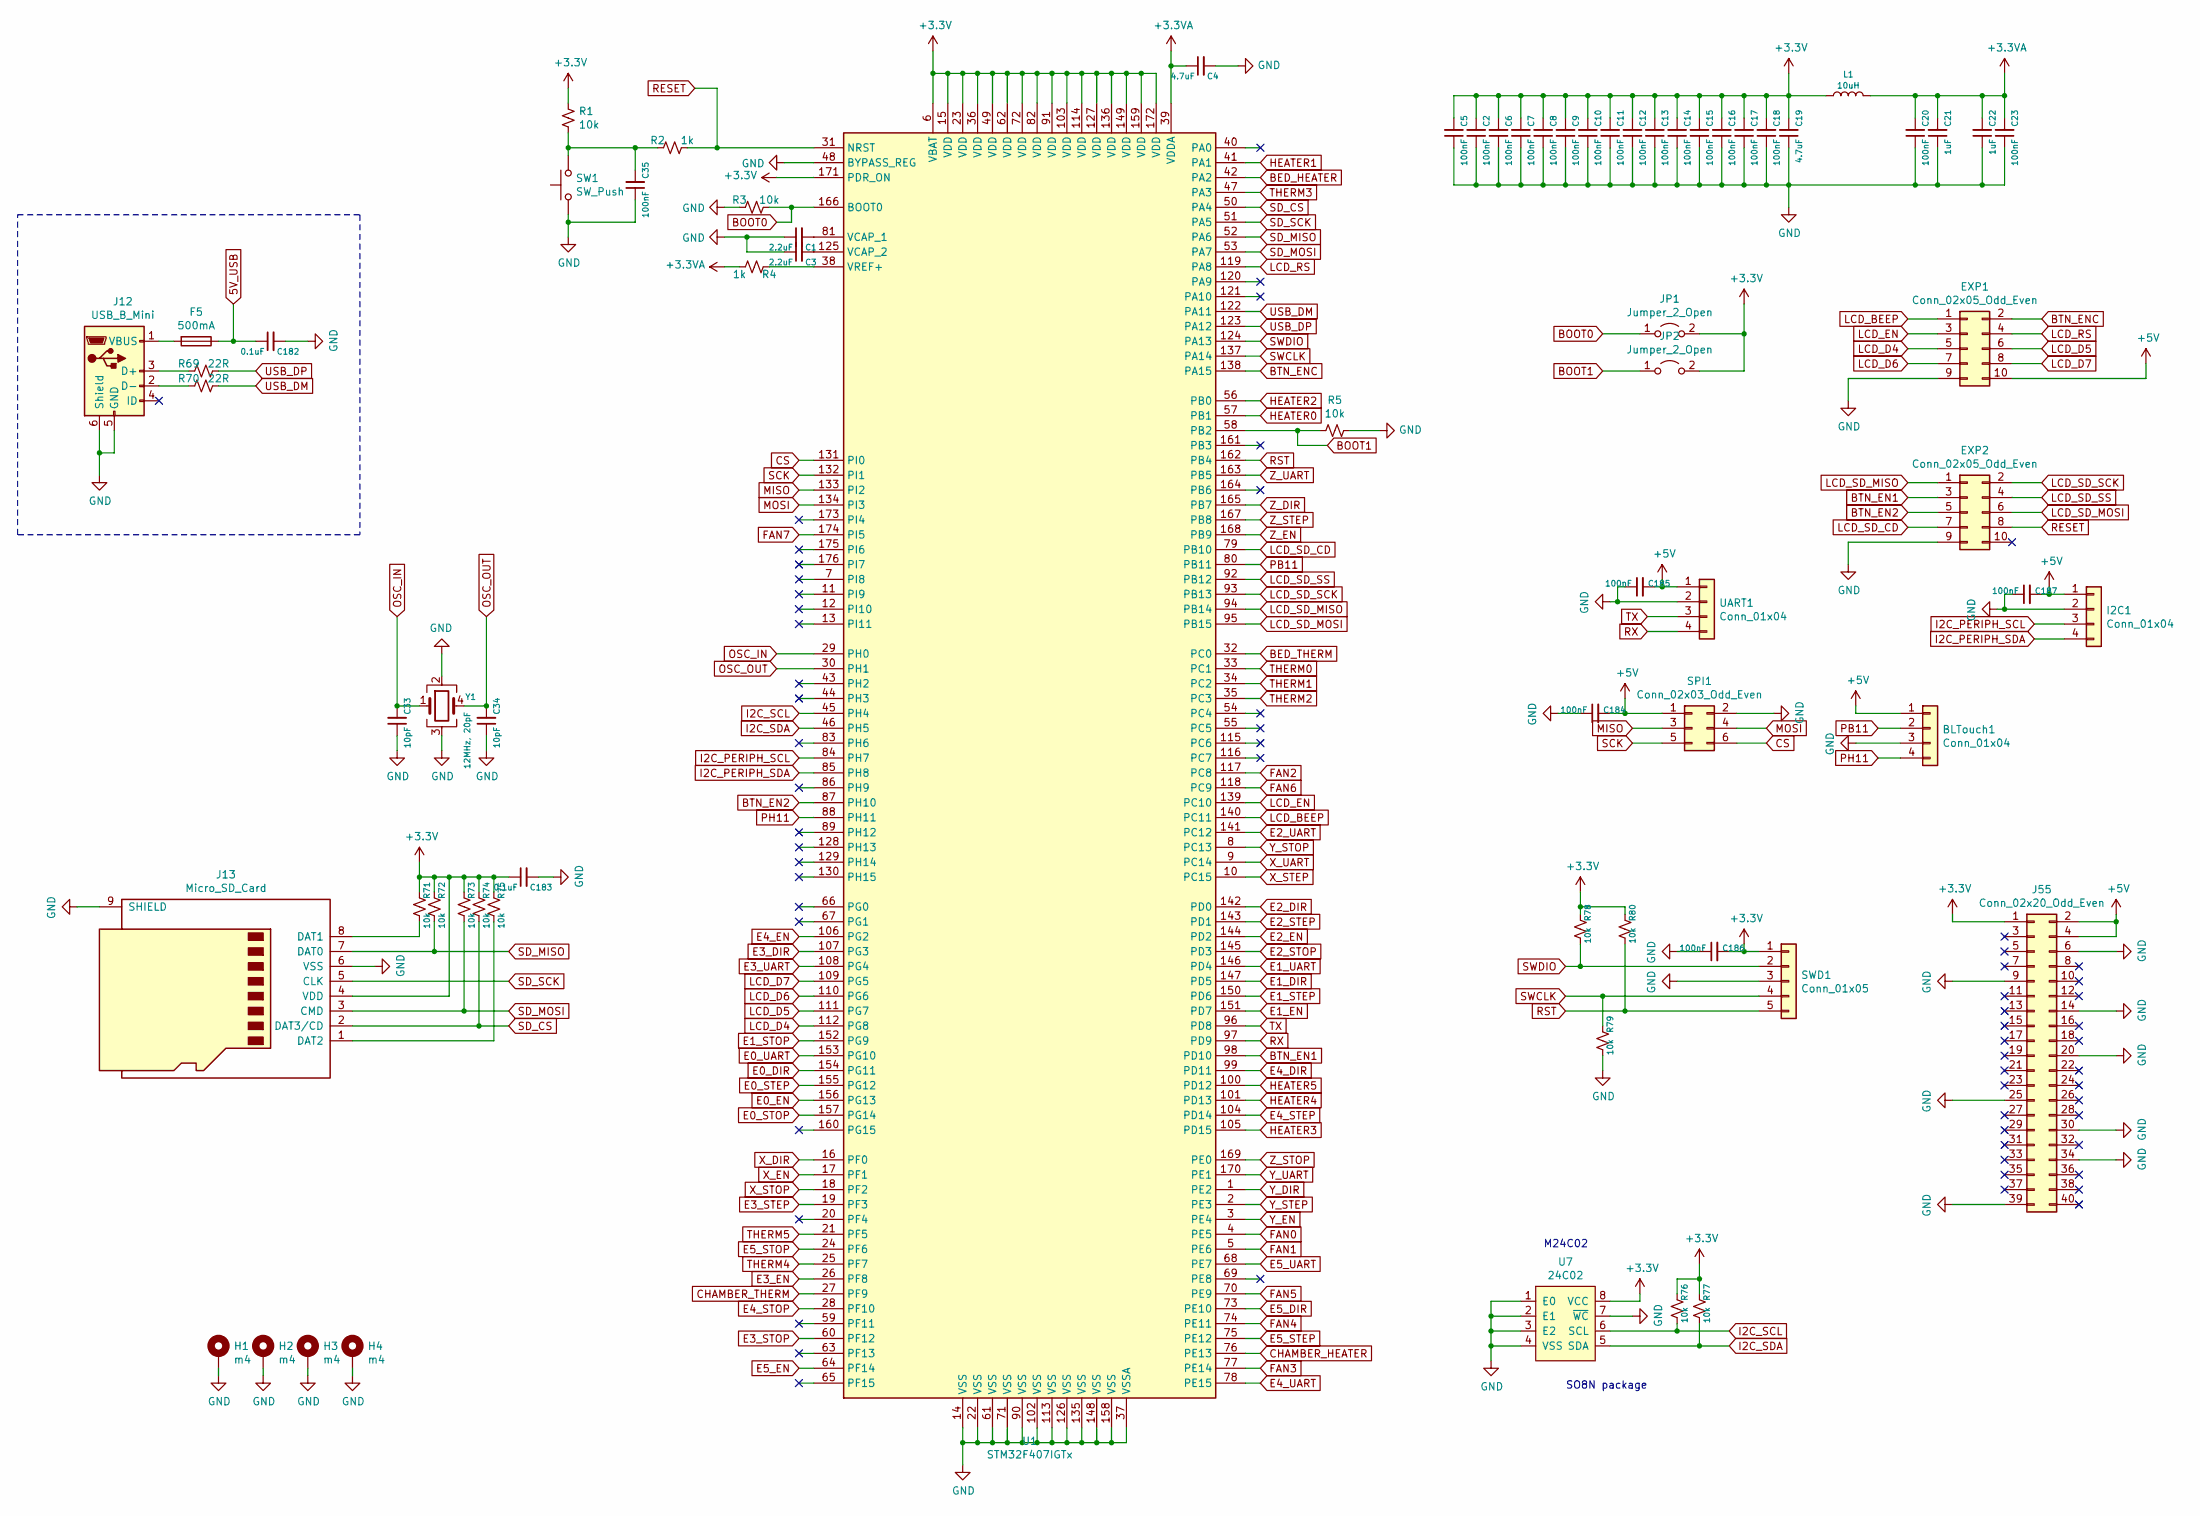
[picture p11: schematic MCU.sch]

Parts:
BLTouch1: Conn_01x04; PinHeader_1x04_P2.54mm_Vertical
C1, C3: 2.2uF; C_0603_1608Metric_Pad1.05x0.95mm_HandSolder
C2, C5, C6, C7, C8, C9, C10, C11, C12, C13, C14, C15, C16, C17, C18, C20, C23, C35, C184, C185, C186, C187: 100nF; C_0603_1608Metric_Pad1.05x0.95mm_HandSolder
C4, C19: 4.7uF; C_0805_2012Metric_Pad1.15x1.40mm_HandSolder
C21, C22: 1uF; C_0603_1608Metric_Pad1.05x0.95mm_HandSolder
C33, C34: 10pF; C_0603_1608Metric_Pad1.05x0.95mm_HandSolder
C182, C183: 0.1uF; C_0603_1608Metric_Pad1.05x0.95mm_HandSolder
EXP1, EXP2: Conn_02x05_Odd_Even; PinHeader_2x05_P2.54mm_Vertical
F5: 500mA; Fuse_1206_3216Metric_Pad1.42x1.75mm_HandSolder
H1, H2, H3, H4: m4; MountingHole_4.3mm_M4_Pad_Via
I2C1: Conn_01x04; PinHeader_1x04_P2.54mm_Vertical
J12: USB_B_Mini; USB_Mini-B_Wuerth_65100516121_Horizontal
J13: Micro_SD_Card; microSD_HC_Wuerth_693072010801
J55: Conn_02x20_Odd_Even; PinHeader_2x20_P2.54mm_Vertical
JP1, JP2: Jumper_2_Open; PinHeader_1x02_P2.54mm_Vertical
L1: 10uH; L_0603_1608Metric_Pad1.05x0.95mm_HandSolder
R1, R3, R5, R71, R72, R73, R74, R75, R76, R77, R78, R79, R80: 10k; R_0603_1608Metric_Pad1.05x0.95mm_HandSolder
R2, R4: 1k; R_0603_1608Metric_Pad1.05x0.95mm_HandSolder
R69, R70: 22R; R_0603_1608Metric_Pad1.05x0.95mm_HandSolder
SPI1: Conn_02x03_Odd_Even; PinHeader_2x03_P2.54mm_Vertical
SW1: SW_Push; SW_Push_1P1T_NO_6x6mm_H9.5mm
SWD1: Conn_01x05; PinHeader_1x05_P2.54mm_Vertical
U1: STM32F407IGTx; LQFP-176_24x24mm_P0.5mm
U7: 24C02; SO-8_3.9x4.9mm_P1.27mm
UART1: Conn_01x04; PinHeader_1x04_P2.54mm_Vertical
Y1: 12MHz, 20pF; Crystal_SMD_EuroQuartz_MJ-4Pin_5.0x3.2mm_HandSoldering

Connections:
5V_USB: C182.1, F5.1; also elsewhere on the board
+3.3VA: C4.1, C20.2, C21.2, C22.2, C23.2, L1.2, R4.2, U1.39 (VDDA); also elsewhere on the board
+3V3: C2.2, C5.2, C6.2, C7.2, C8.2, C9.2, C10.2, C11.2, C12.2, C13.2, C14.2, C15.2, C16.2, C17.2, C18.2, C19.2, C183.1, C186.2, J13.4 (VDD), J55.1, JP1.2 (B), JP2.2 (B), L1.1, R1.1, R71.1, R72.1, R73.1, R74.1, R75.1, R76.1, R77.1, R78.1, R80.1, SWD1.1, U1.6 (VBAT), U1.15 (VDD), U1.23 (VDD), U1.36 (VDD), U1.49 (VDD), U1.62 (VDD), U1.72 (VDD), U1.82 (VDD), U1.91 (VDD), U1.103 (VDD), U1.114 (VDD), U1.127 (VDD), U1.136 (VDD), U1.149 (VDD), U1.159 (VDD), U1.171 (PDR_ON), U1.172 (VDD), U7.8 (VCC); also elsewhere on the board
+5V: BLTouch1.1, C184.2, C185.2, C187.2, EXP1.10, I2C1.1, J55.2, J55.4, SPI1.1, UART1.1; also elsewhere on the board
BED_HEATER: U1.42 (PA2); also elsewhere on the board
BED_THERM: U1.32 (PC0); also elsewhere on the board
BOOT0: JP1.1 (A), R3.1, U1.166 (BOOT0)
BOOT1: JP2.1 (A), R5.2, U1.58 (PB2)
BTN_EN1: EXP2.3, U1.98 (PD10)
BTN_EN2: EXP2.5, U1.87 (PH10)
BTN_ENC: EXP1.2, U1.138 (PA15)
CHAMBER_HEATER: U1.76 (PE13); also elsewhere on the board
CHAMBER_THERM: U1.27 (PF9); also elsewhere on the board
CS: SPI1.6, U1.131 (PI0)
E0_DIR: U1.154 (PG11); also elsewhere on the board
E0_EN: U1.156 (PG13); also elsewhere on the board
E0_STEP: U1.155 (PG12); also elsewhere on the board
E0_STOP: U1.157 (PG14); also elsewhere on the board
E0_UART: U1.153 (PG10); also elsewhere on the board
E1_DIR: U1.147 (PD5); also elsewhere on the board
E1_EN: U1.151 (PD7); also elsewhere on the board
E1_STEP: U1.150 (PD6); also elsewhere on the board
E1_STOP: U1.152 (PG9); also elsewhere on the board
E1_UART: U1.146 (PD4); also elsewhere on the board
E2_DIR: U1.142 (PD0); also elsewhere on the board
E2_EN: U1.144 (PD2); also elsewhere on the board
E2_STEP: U1.143 (PD1); also elsewhere on the board
E2_STOP: U1.145 (PD3); also elsewhere on the board
E2_UART: U1.141 (PC12); also elsewhere on the board
E3_DIR: U1.107 (PG3); also elsewhere on the board
E3_EN: U1.26 (PF8); also elsewhere on the board
E3_STEP: U1.19 (PF3); also elsewhere on the board
E3_STOP: U1.60 (PF12); also elsewhere on the board
E3_UART: U1.108 (PG4); also elsewhere on the board
E4_DIR: U1.99 (PD11); also elsewhere on the board
E4_EN: U1.106 (PG2); also elsewhere on the board
E4_STEP: U1.104 (PD14); also elsewhere on the board
E4_STOP: U1.28 (PF10); also elsewhere on the board
E4_UART: U1.78 (PE15); also elsewhere on the board
E5_DIR: U1.73 (PE10); also elsewhere on the board
E5_EN: U1.64 (PF14); also elsewhere on the board
E5_STEP: U1.75 (PE12); also elsewhere on the board
E5_STOP: U1.24 (PF6); also elsewhere on the board
E5_UART: U1.68 (PE7); also elsewhere on the board
FAN0: U1.4 (PE5); also elsewhere on the board
FAN1: U1.5 (PE6); also elsewhere on the board
FAN2: U1.117 (PC8); also elsewhere on the board
FAN3: U1.77 (PE14); also elsewhere on the board
FAN4: U1.74 (PE11); also elsewhere on the board
FAN5: U1.70 (PE9); also elsewhere on the board
FAN6: U1.118 (PC9); also elsewhere on the board
FAN7: U1.174 (PI5); also elsewhere on the board
GND: BLTouch1.3, C1.1, C2.1, C3.1, C4.2, C5.1, C6.1, C7.1, C8.1, C9.1, C10.1, C11.1, C12.1, C13.1, C14.1, C15.1, C16.1, C17.1, C18.1, C19.1, C20.1, C21.1, C22.1, C23.1, C33.1, C34.1, C35.1, C182.2, C183.2, C184.1, C185.1, C186.1, C187.1, EXP1.9, EXP2.9, H1.1, H2.1, H3.1, H4.1, I2C1.2, J12.5 (GND), J12.6 (Shield), J13.6 (VSS), J13.9 (SHIELD), J55.6, J55.9, J55.14, J55.20, J55.25, J55.30, J55.34, J55.39, R3.2, R5.1, R79.2, SPI1.2, SW1.1, SWD1.3, U1.14 (VSS), U1.22 (VSS), U1.37 (VSSA), U1.48 (BYPASS_REG), U1.61 (VSS), U1.71 (VSS), U1.90 (VSS), U1.102 (VSS), U1.113 (VSS), U1.126 (VSS), U1.135 (VSS), U1.148 (VSS), U1.158 (VSS), U7.1 (E0), U7.2 (E1), U7.3 (E2), U7.4 (VSS), U7.7 (~WC), UART1.2, Y1.2, Y1.3; also elsewhere on the board
HEATER0: U1.57 (PB1); also elsewhere on the board
HEATER1: U1.41 (PA1); also elsewhere on the board
HEATER2: U1.56 (PB0); also elsewhere on the board
HEATER3: U1.105 (PD15); also elsewhere on the board
HEATER4: U1.101 (PD13); also elsewhere on the board
HEATER5: U1.100 (PD12); also elsewhere on the board
I2C_PERIPH_SCL: I2C1.3, U1.84 (PH7)
I2C_PERIPH_SDA: I2C1.4, U1.85 (PH8)
I2C_SCL: R76.2, U1.45 (PH4), U7.6 (SCL)
I2C_SDA: R77.2, U1.46 (PH5), U7.5 (SDA)
LCD_BEEP: EXP1.1, U1.140 (PC11)
LCD_D4: EXP1.5, U1.112 (PG8)
LCD_D5: EXP1.6, U1.111 (PG7)
LCD_D6: EXP1.7, U1.110 (PG6)
LCD_D7: EXP1.8, U1.109 (PG5)
LCD_EN: EXP1.3, U1.139 (PC10)
LCD_RS: EXP1.4, U1.119 (PA8)
LCD_SD_CD: EXP2.7, U1.79 (PB10)
LCD_SD_MISO: EXP2.1, U1.94 (PB14)
LCD_SD_MOSI: EXP2.6, U1.95 (PB15)
LCD_SD_SCK: EXP2.2, U1.93 (PB13)
LCD_SD_SS: EXP2.4, U1.92 (PB12)
MISO: SPI1.3, U1.133 (PI2)
MOSI: SPI1.4, U1.134 (PI3)
unnamed: C1.2, U1.81 (VCAP_1)
unnamed: C3.2, U1.125 (VCAP_2)
unnamed: C35.2, R1.2, R2.2, SW1.2
unnamed: F5.2, J12.1 (VBUS)
unnamed: J12.2 (D-), R70.2
unnamed: J12.3 (D+), R69.2
unnamed: J13.1 (DAT2), R75.2
unnamed: J13.8 (DAT1), R71.2
unnamed: R4.1, U1.38 (VREF+)
OSC_IN: C33.2, U1.29 (PH0), Y1.1
OSC_OUT: C34.2, U1.30 (PH1), Y1.4
PB11: BLTouch1.2, U1.80 (PB11)
PH11: BLTouch1.4, U1.88 (PH11)
RESET: EXP2.8, R2.1, U1.31 (NRST)
RST: R80.2, SWD1.5, U1.162 (PB4)
RX: U1.97 (PD9), UART1.4
SCK: SPI1.5, U1.132 (PI1)
SD_CS: J13.2 (DAT3/CD), R74.2, U1.50 (PA4)
SD_MISO: J13.7 (DAT0), R72.2, U1.52 (PA6)
SD_MOSI: J13.3 (CMD), R73.2, U1.53 (PA7)
SD_SCK: J13.5 (CLK), U1.51 (PA5)
SWCLK: R79.1, SWD1.4, U1.137 (PA14)
SWDIO: R78.2, SWD1.2, U1.124 (PA13)
THERM0: U1.33 (PC1); also elsewhere on the board
THERM1: U1.34 (PC2); also elsewhere on the board
THERM2: U1.35 (PC3); also elsewhere on the board
THERM3: U1.47 (PA3); also elsewhere on the board
THERM4: U1.25 (PF7); also elsewhere on the board
THERM5: U1.21 (PF5); also elsewhere on the board
TX: U1.96 (PD8), UART1.3
USB_DM: R70.1, U1.122 (PA11)
USB_DP: R69.1, U1.123 (PA12)
X_DIR: U1.16 (PF0); also elsewhere on the board
X_EN: U1.17 (PF1); also elsewhere on the board
X_STEP: U1.10 (PC15); also elsewhere on the board
X_STOP: U1.18 (PF2); also elsewhere on the board
X_UART: U1.9 (PC14); also elsewhere on the board
Y_DIR: U1.1 (PE2); also elsewhere on the board
Y_EN: U1.3 (PE4); also elsewhere on the board
Y_STEP: U1.2 (PE3); also elsewhere on the board
Y_STOP: U1.8 (PC13); also elsewhere on the board
Y_UART: U1.170 (PE1); also elsewhere on the board
Z_DIR: U1.165 (PB7); also elsewhere on the board
Z_EN: U1.168 (PB9); also elsewhere on the board
Z_STEP: U1.167 (PB8); also elsewhere on the board
Z_STOP: U1.169 (PE0); also elsewhere on the board
Z_UART: U1.163 (PB5); also elsewhere on the board

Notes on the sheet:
M24C02
SO8N package

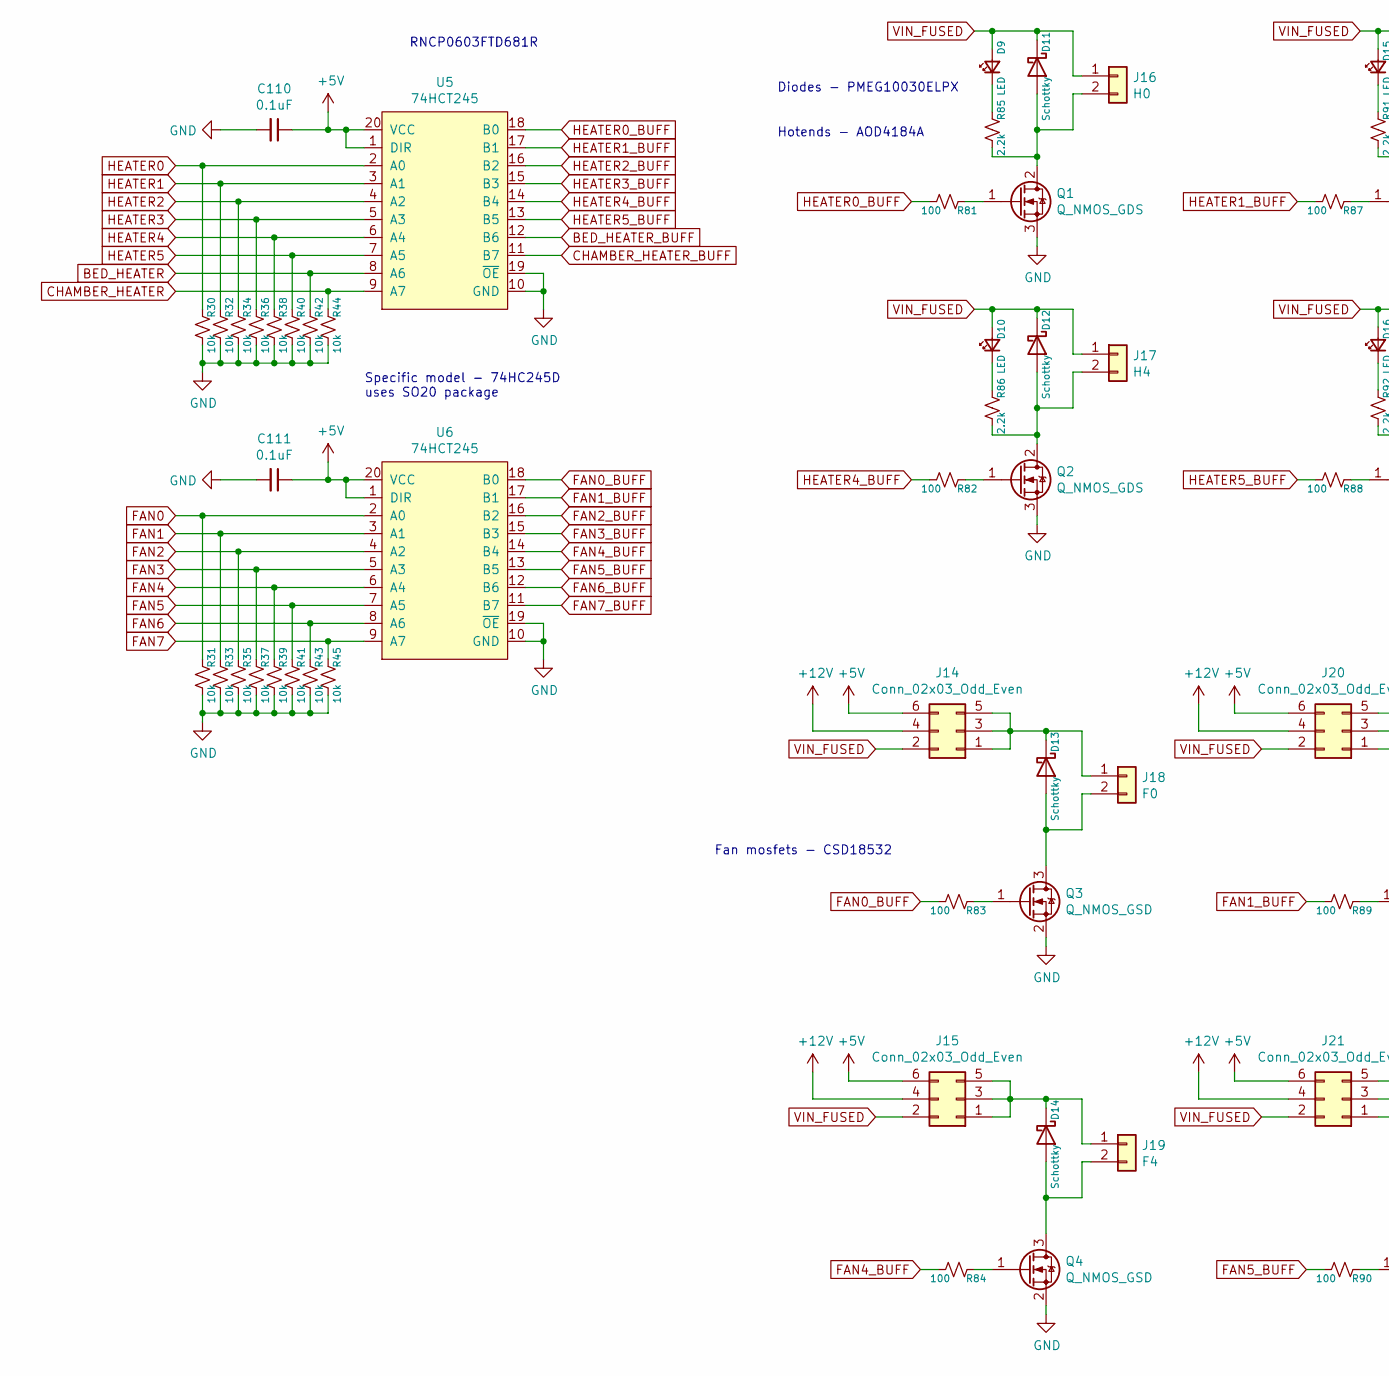
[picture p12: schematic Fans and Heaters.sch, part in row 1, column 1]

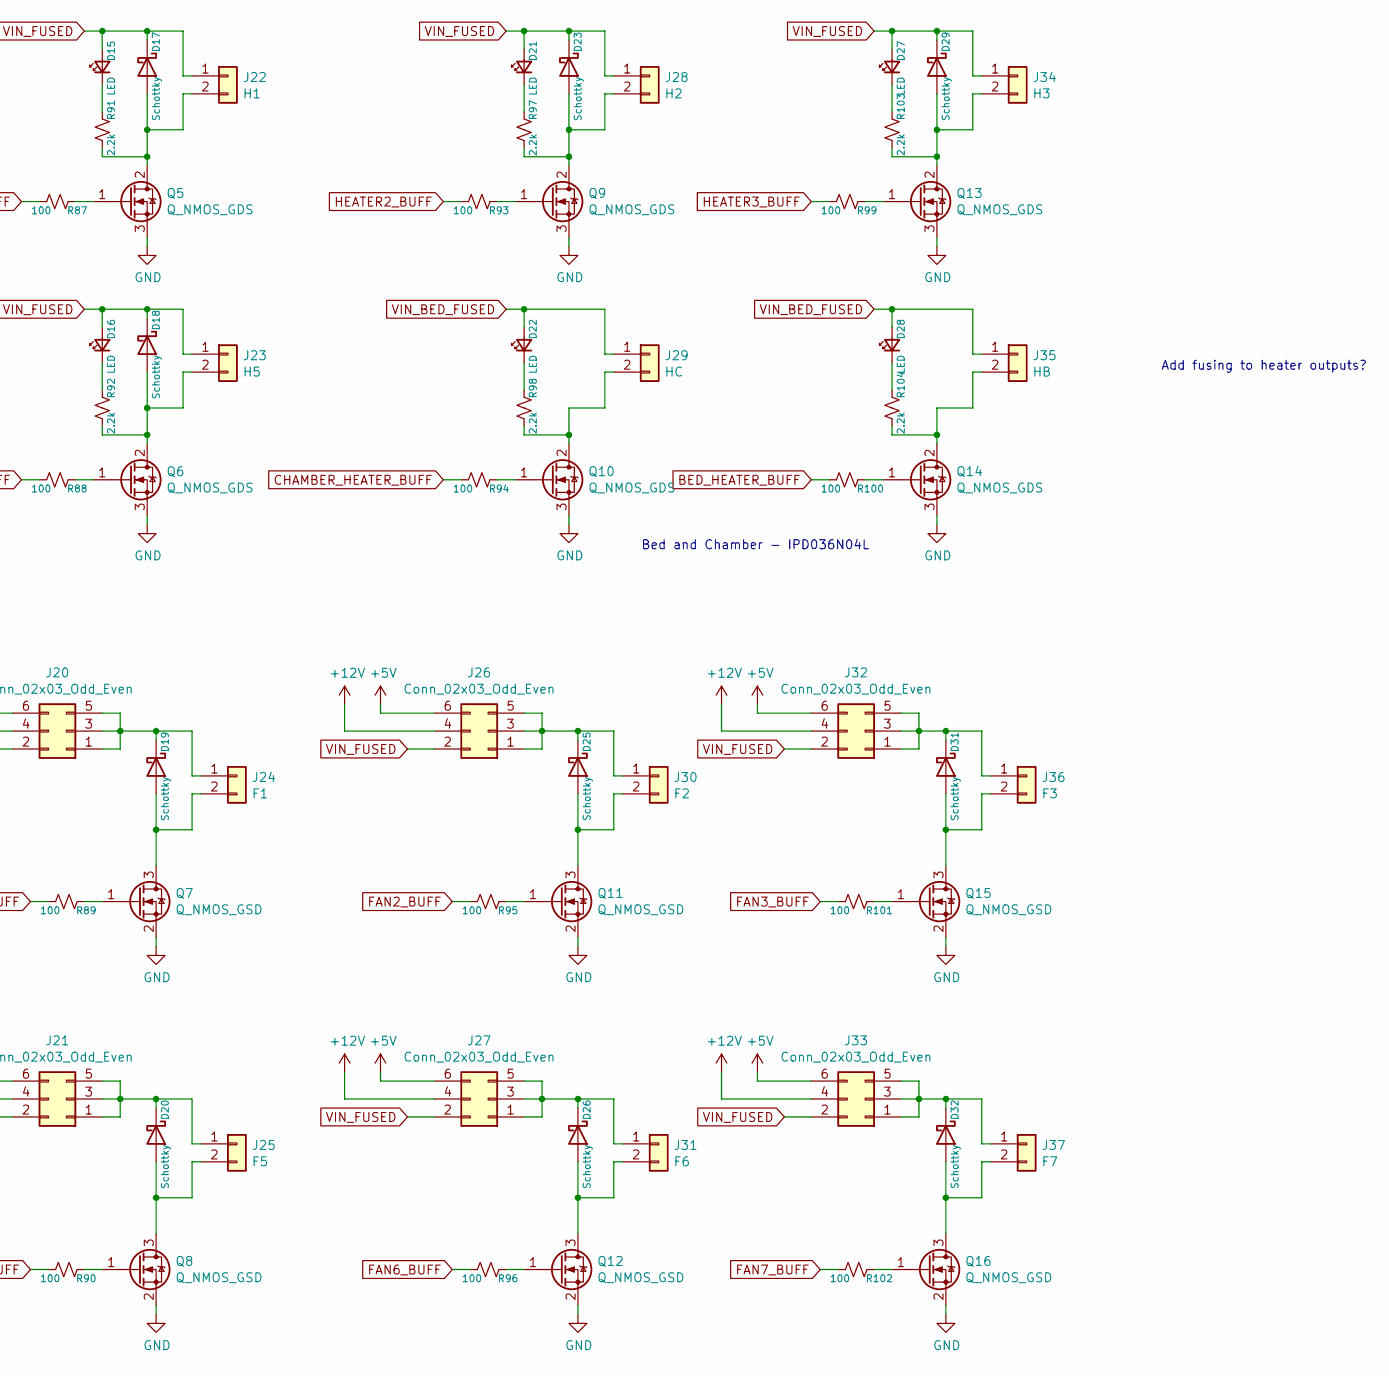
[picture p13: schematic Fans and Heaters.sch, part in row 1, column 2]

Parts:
C110, C111: 0.1uF; C_0603_1608Metric_Pad1.05x0.95mm_HandSolder
D9, D10, D15, D16, D21, D22, D27, D28: LED; LED_0603_1608Metric_Pad1.05x0.95mm_HandSolder
D11, D12, D13, D14, D17, D18, D19, D20, D23, D25, D26, D29, D31, D32: Schottky; D_SOD-128
J14, J15, J20, J21, J26, J27, J32, J33: Conn_02x03_Odd_Even; PinHeader_2x03_P2.54mm_Vertical
J16: H0; TerminalBlock_Phoenix_MKDS-1,5-2_1x02_P5.00mm_Horizontal
J17: H4; TerminalBlock_Phoenix_MKDS-1,5-2_1x02_P5.00mm_Horizontal
J18: F0; Molex_KK-254_AE-6410-02A_1x02_P2.54mm_Vertical
J19: F4; Molex_KK-254_AE-6410-02A_1x02_P2.54mm_Vertical
J22: H1; TerminalBlock_Phoenix_MKDS-1,5-2_1x02_P5.00mm_Horizontal
J23: H5; TerminalBlock_Phoenix_MKDS-1,5-2_1x02_P5.00mm_Horizontal
J24: F1; Molex_KK-254_AE-6410-02A_1x02_P2.54mm_Vertical
J25: F5; Molex_KK-254_AE-6410-02A_1x02_P2.54mm_Vertical
J28: H2; TerminalBlock_Phoenix_MKDS-1,5-2_1x02_P5.00mm_Horizontal
J29: HC; TerminalBlock_Dinkle_DT-55-B01X-02_P10.00mm
J30: F2; Molex_KK-254_AE-6410-02A_1x02_P2.54mm_Vertical
J31: F6; Molex_KK-254_AE-6410-02A_1x02_P2.54mm_Vertical
J34: H3; TerminalBlock_Phoenix_MKDS-1,5-2_1x02_P5.00mm_Horizontal
J35: HB; TerminalBlock_Dinkle_DT-55-B01X-02_P10.00mm
J36: F3; Molex_KK-254_AE-6410-02A_1x02_P2.54mm_Vertical
J37: F7; Molex_KK-254_AE-6410-02A_1x02_P2.54mm_Vertical
Q1, Q2, Q5, Q6, Q9, Q10, Q13, Q14: Q_NMOS_GDS; TO-252-2
Q3, Q4, Q7, Q8, Q11, Q12, Q15, Q16: Q_NMOS_GSD; SOT-23_Handsoldering
R30, R31, R32, R33, R34, R35, R36, R37, R38, R39, R40, R41, R42, R43, R44, R45: 10k; R_0603_1608Metric_Pad1.05x0.95mm_HandSolder
R81, R82, R83, R84, R87, R88, R89, R90, R93, R94, R95, R96, R99, R100, R101, R102: 100; R_0603_1608Metric_Pad1.05x0.95mm_HandSolder
R85, R86, R91, R92, R97, R98, R103, R104: 2.2k; R_0603_1608Metric_Pad1.05x0.95mm_HandSolder
U5, U6: 74HCT245; SO-20_12.8x7.5mm_P1.27mm

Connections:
+5V: C110.1, C111.1, J14.6, J15.6, J20.6, J21.6, J26.6, J27.6, J32.6, J33.6, U5.1 (DIR), U5.20 (VCC), U6.1 (DIR), U6.20 (VCC); also elsewhere on the board
+12V: J14.4, J15.4, J20.4, J21.4, J26.4, J27.4, J32.4, J33.4; also elsewhere on the board
BED_HEATER: R42.1, U5.8 (A6); also elsewhere on the board
BED_HEATER_BUFF: R100.2, U5.12 (B6)
CHAMBER_HEATER: R44.1, U5.9 (A7); also elsewhere on the board
CHAMBER_HEATER_BUFF: R94.2, U5.11 (B7)
FAN0: R31.1, U6.2 (A0); also elsewhere on the board
FAN0_BUFF: R83.2, U6.18 (B0)
FAN1: R33.1, U6.3 (A1); also elsewhere on the board
FAN1_BUFF: R89.2, U6.17 (B1)
FAN2: R35.1, U6.4 (A2); also elsewhere on the board
FAN2_BUFF: R95.2, U6.16 (B2)
FAN3: R37.1, U6.5 (A3); also elsewhere on the board
FAN3_BUFF: R101.2, U6.15 (B3)
FAN4: R39.1, U6.6 (A4); also elsewhere on the board
FAN4_BUFF: R84.2, U6.14 (B4)
FAN5: R41.1, U6.7 (A5); also elsewhere on the board
FAN5_BUFF: R90.2, U6.13 (B5)
FAN6: R43.1, U6.8 (A6); also elsewhere on the board
FAN6_BUFF: R96.2, U6.12 (B6)
FAN7: R45.1, U6.9 (A7); also elsewhere on the board
FAN7_BUFF: R102.2, U6.11 (B7)
GND: C110.2, C111.2, Q1.3 (S), Q2.3 (S), Q3.2 (S), Q4.2 (S), Q5.3 (S), Q6.3 (S), Q7.2 (S), Q8.2 (S), Q9.3 (S), Q10.3 (S), Q11.2 (S), Q12.2 (S), Q13.3 (S), Q14.3 (S), Q15.2 (S), Q16.2 (S), R30.2, R31.2, R32.2, R33.2, R34.2, R35.2, R36.2, R37.2, R38.2, R39.2, R40.2, R41.2, R42.2, R43.2, R44.2, R45.2, U5.10 (GND), U5.19 (~OE), U6.10 (GND), U6.19 (~OE); also elsewhere on the board
HEATER0: R30.1, U5.2 (A0); also elsewhere on the board
HEATER0_BUFF: R81.2, U5.18 (B0)
HEATER1: R32.1, U5.3 (A1); also elsewhere on the board
HEATER1_BUFF: R87.2, U5.17 (B1)
HEATER2: R34.1, U5.4 (A2); also elsewhere on the board
HEATER2_BUFF: R93.2, U5.16 (B2)
HEATER3: R36.1, U5.5 (A3); also elsewhere on the board
HEATER3_BUFF: R99.2, U5.15 (B3)
HEATER4: R38.1, U5.6 (A4); also elsewhere on the board
HEATER4_BUFF: R82.2, U5.14 (B4)
HEATER5: R40.1, U5.7 (A5); also elsewhere on the board
HEATER5_BUFF: R88.2, U5.13 (B5)
unnamed: D9.1 (K), R85.1
unnamed: D10.1 (K), R86.1
unnamed: D11.2 (A), J16.2, Q1.2 (D), R85.2
unnamed: D12.2 (A), J17.2, Q2.2 (D), R86.2
unnamed: D13.1 (K), J14.1, J14.3, J14.5, J18.1
unnamed: D13.2 (A), J18.2, Q3.3 (D)
unnamed: D14.1 (K), J15.1, J15.3, J15.5, J19.1
unnamed: D14.2 (A), J19.2, Q4.3 (D)
unnamed: D15.1 (K), R91.1
unnamed: D16.1 (K), R92.1
unnamed: D17.2 (A), J22.2, Q5.2 (D), R91.2
unnamed: D18.2 (A), J23.2, Q6.2 (D), R92.2
unnamed: D19.1 (K), J20.1, J20.3, J20.5, J24.1
unnamed: D19.2 (A), J24.2, Q7.3 (D)
unnamed: D20.1 (K), J21.1, J21.3, J21.5, J25.1
unnamed: D20.2 (A), J25.2, Q8.3 (D)
unnamed: D21.1 (K), R97.1
unnamed: D22.1 (K), R98.1
unnamed: D23.2 (A), J28.2, Q9.2 (D), R97.2
unnamed: D25.1 (K), J26.1, J26.3, J26.5, J30.1
unnamed: D25.2 (A), J30.2, Q11.3 (D)
unnamed: D26.1 (K), J27.1, J27.3, J27.5, J31.1
unnamed: D26.2 (A), J31.2, Q12.3 (D)
unnamed: D27.1 (K), R103.1
unnamed: D28.1 (K), R104.1
unnamed: D29.2 (A), J34.2, Q13.2 (D), R103.2
unnamed: D31.1 (K), J32.1, J32.3, J32.5, J36.1
unnamed: D31.2 (A), J36.2, Q15.3 (D)
unnamed: D32.1 (K), J33.1, J33.3, J33.5, J37.1
unnamed: D32.2 (A), J37.2, Q16.3 (D)
unnamed: J29.2, Q10.2 (D), R98.2
unnamed: J35.2, Q14.2 (D), R104.2
unnamed: Q1.1 (G), R81.1
unnamed: Q2.1 (G), R82.1
unnamed: Q3.1 (G), R83.1
unnamed: Q4.1 (G), R84.1
unnamed: Q5.1 (G), R87.1
unnamed: Q6.1 (G), R88.1
unnamed: Q7.1 (G), R89.1
unnamed: Q8.1 (G), R90.1
unnamed: Q9.1 (G), R93.1
unnamed: Q10.1 (G), R94.1
unnamed: Q11.1 (G), R95.1
unnamed: Q12.1 (G), R96.1
unnamed: Q13.1 (G), R99.1
unnamed: Q14.1 (G), R100.1
unnamed: Q15.1 (G), R101.1
unnamed: Q16.1 (G), R102.1
VIN_BED_FUSED: D22.2 (A), D28.2 (A), J29.1, J35.1; also elsewhere on the board
VIN_FUSED: D9.2 (A), D10.2 (A), D11.1 (K), D12.1 (K), D15.2 (A), D16.2 (A), D17.1 (K), D18.1 (K), D21.2 (A), D23.1 (K), D27.2 (A), D29.1 (K), J14.2, J15.2, J16.1, J17.1, J20.2, J21.2, J22.1, J23.1, J26.2, J27.2, J28.1, J32.2, J33.2, J34.1; also elsewhere on the board

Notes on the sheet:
Add fusing to heater outputs?
Diodes - PMEG10030ELPX
RNCP0603FTD681R
Fan mosfets - CSD18532
Bed and Chamber - IPD036N04L
Hotends - AOD4184A
Specific model - 74HC245D uses SO20 package

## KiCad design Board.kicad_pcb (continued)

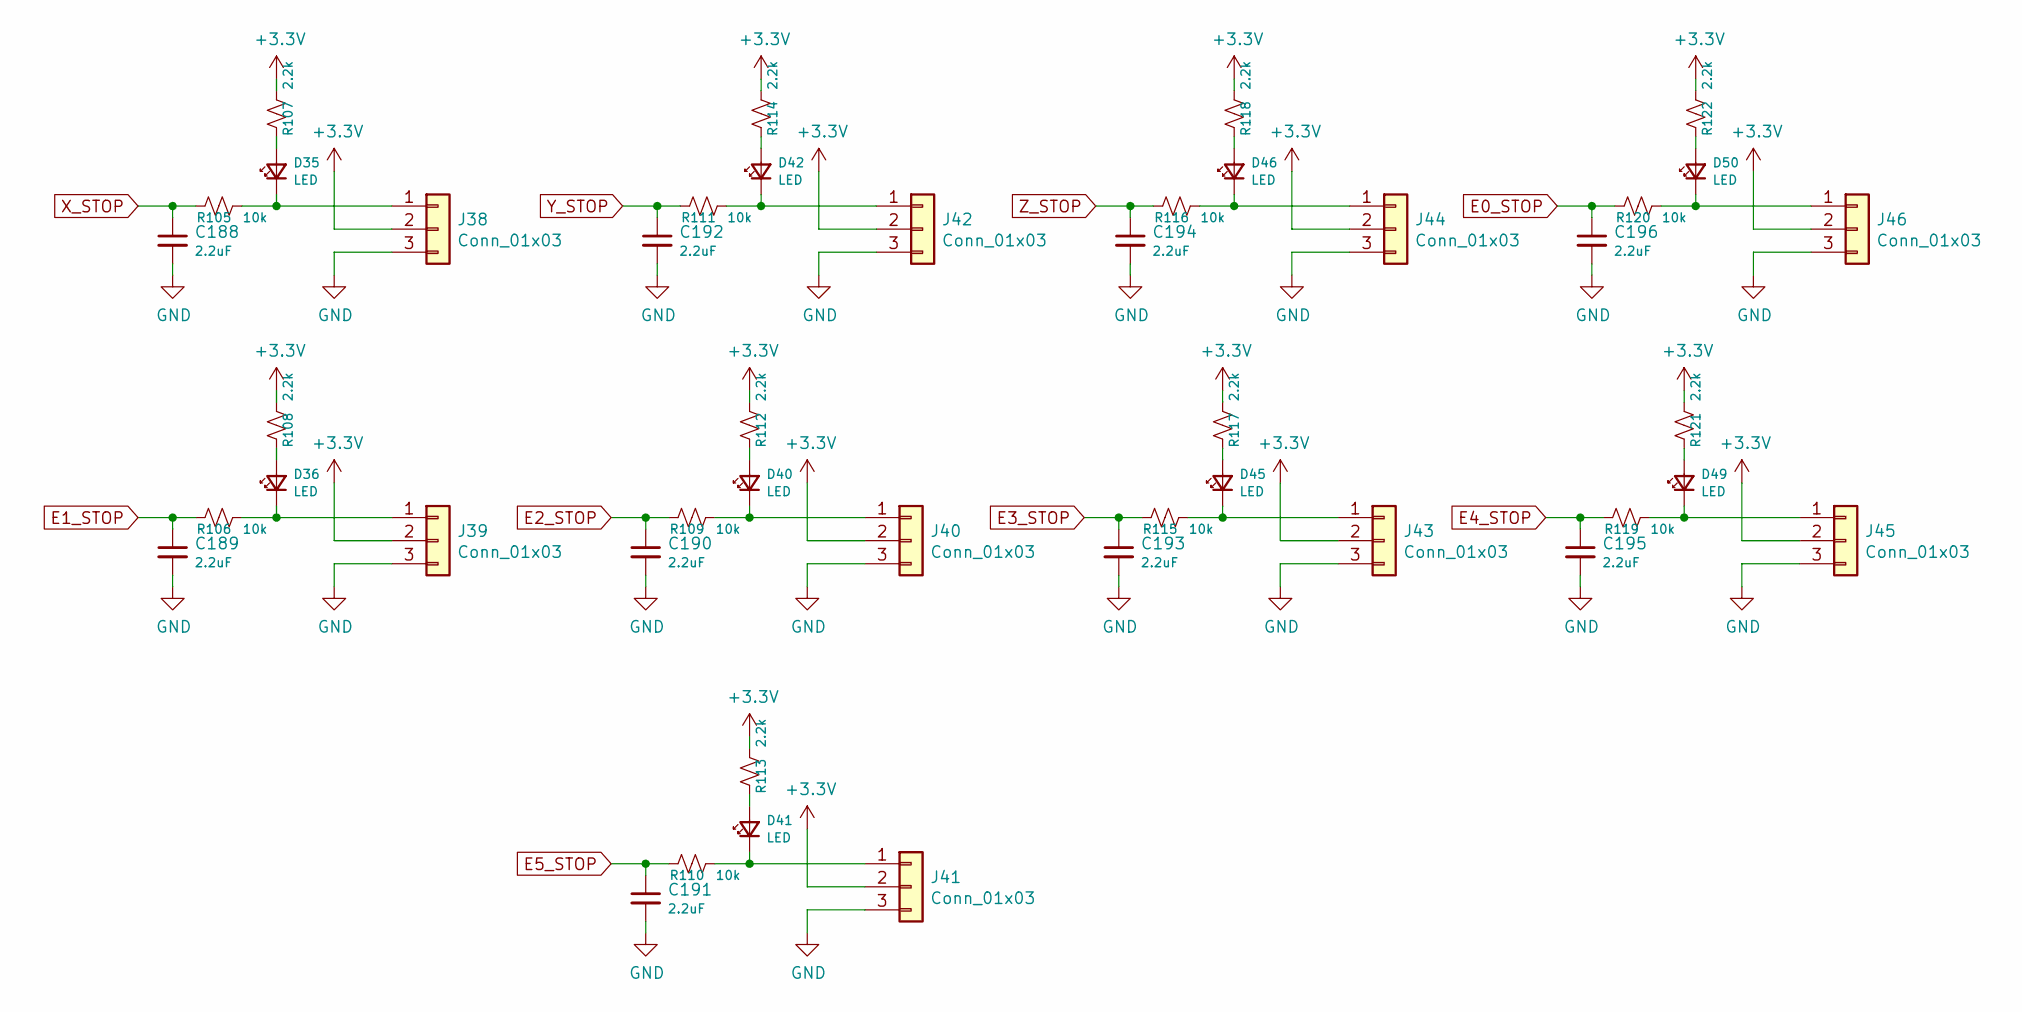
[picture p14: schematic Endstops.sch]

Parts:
C188, C189, C190, C191, C192, C193, C194, C195, C196: 2.2uF; C_0603_1608Metric_Pad1.05x0.95mm_HandSolder
D35, D36, D40, D41, D42, D45, D46, D49, D50: LED; LED_0603_1608Metric_Pad1.05x0.95mm_HandSolder
J38, J39, J40, J41, J42, J43, J44, J45, J46: Conn_01x03; Molex_KK-254_AE-6410-03A_1x03_P2.54mm_Vertical
R105, R106, R109, R110, R111, R115, R116, R119, R120: 10k; R_0603_1608Metric_Pad1.05x0.95mm_HandSolder
R107, R108, R112, R113, R114, R117, R118, R121, R122: 2.2k; R_0603_1608Metric_Pad1.05x0.95mm_HandSolder

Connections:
+3V3: J38.2, J39.2, J40.2, J41.2, J42.2, J43.2, J44.2, J45.2, J46.2, R107.1, R108.1, R112.1, R113.1, R114.1, R117.1, R118.1, R121.1, R122.1; also elsewhere on the board
E0_STOP: C196.1, R120.2; also elsewhere on the board
E1_STOP: C189.1, R106.2; also elsewhere on the board
E2_STOP: C190.1, R109.2; also elsewhere on the board
E3_STOP: C193.1, R115.2; also elsewhere on the board
E4_STOP: C195.1, R119.2; also elsewhere on the board
E5_STOP: C191.1, R110.2; also elsewhere on the board
GND: C188.2, C189.2, C190.2, C191.2, C192.2, C193.2, C194.2, C195.2, C196.2, J38.3, J39.3, J40.3, J41.3, J42.3, J43.3, J44.3, J45.3, J46.3; also elsewhere on the board
unnamed: D35.1 (K), J38.1, R105.1
unnamed: D35.2 (A), R107.2
unnamed: D36.1 (K), J39.1, R106.1
unnamed: D36.2 (A), R108.2
unnamed: D40.1 (K), J40.1, R109.1
unnamed: D40.2 (A), R112.2
unnamed: D41.1 (K), J41.1, R110.1
unnamed: D41.2 (A), R113.2
unnamed: D42.1 (K), J42.1, R111.1
unnamed: D42.2 (A), R114.2
unnamed: D45.1 (K), J43.1, R115.1
unnamed: D45.2 (A), R117.2
unnamed: D46.1 (K), J44.1, R116.1
unnamed: D46.2 (A), R118.2
unnamed: D49.1 (K), J45.1, R119.1
unnamed: D49.2 (A), R121.2
unnamed: D50.1 (K), J46.1, R120.1
unnamed: D50.2 (A), R122.2
X_STOP: C188.1, R105.2; also elsewhere on the board
Y_STOP: C192.1, R111.2; also elsewhere on the board
Z_STOP: C194.1, R116.2; also elsewhere on the board

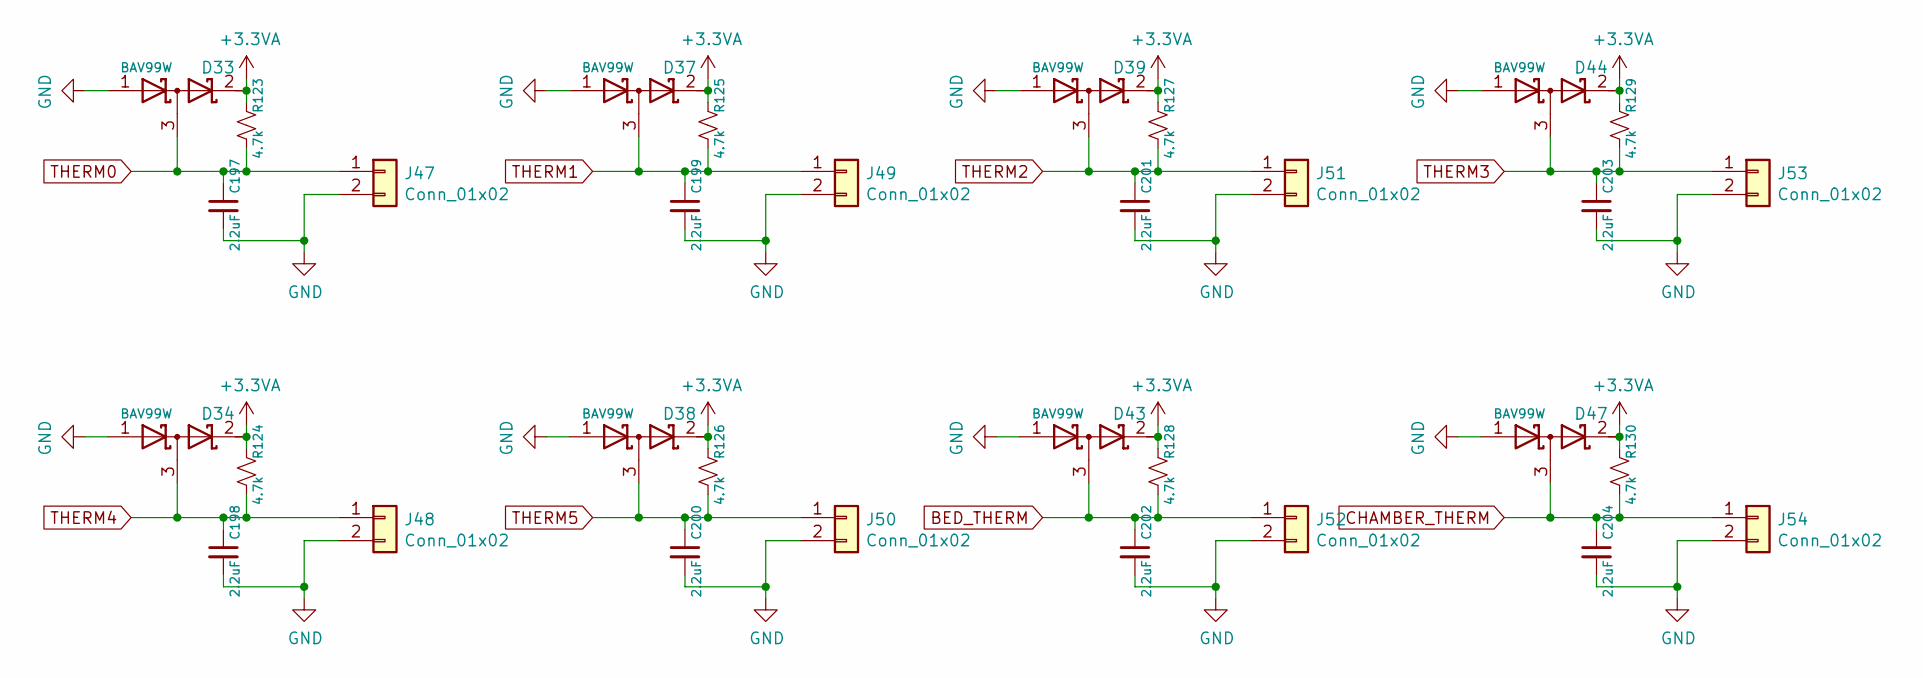
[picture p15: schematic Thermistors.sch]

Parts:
C197, C198, C199, C200, C201, C202, C203, C204: 2.2uF; C_0603_1608Metric_Pad1.05x0.95mm_HandSolder
D33, D34, D37, D38, D39, D43, D44, D47: BAV99W; SOT-323_SC-70_Handsoldering
J47, J48, J49, J50, J51, J52, J53, J54: Conn_01x02; Molex_KK-254_AE-6410-02A_1x02_P2.54mm_Vertical
R123, R124, R125, R126, R127, R128, R129, R130: 4.7k; R_0603_1608Metric_Pad1.05x0.95mm_HandSolder

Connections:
+3.3VA: D33.2 (K), D34.2 (K), D37.2 (K), D38.2 (K), D39.2 (K), D43.2 (K), D44.2 (K), D47.2 (K), R123.1, R124.1, R125.1, R126.1, R127.1, R128.1, R129.1, R130.1; also elsewhere on the board
BED_THERM: C202.1, D43.3 (common), J52.1, R128.2; also elsewhere on the board
CHAMBER_THERM: C204.1, D47.3 (common), J54.1, R130.2; also elsewhere on the board
GND: C197.2, C198.2, C199.2, C200.2, C201.2, C202.2, C203.2, C204.2, D33.1 (A), D34.1 (A), D37.1 (A), D38.1 (A), D39.1 (A), D43.1 (A), D44.1 (A), D47.1 (A), J47.2, J48.2, J49.2, J50.2, J51.2, J52.2, J53.2, J54.2; also elsewhere on the board
THERM0: C197.1, D33.3 (common), J47.1, R123.2; also elsewhere on the board
THERM1: C199.1, D37.3 (common), J49.1, R125.2; also elsewhere on the board
THERM2: C201.1, D39.3 (common), J51.1, R127.2; also elsewhere on the board
THERM3: C203.1, D44.3 (common), J53.1, R129.2; also elsewhere on the board
THERM4: C198.1, D34.3 (common), J48.1, R124.2; also elsewhere on the board
THERM5: C200.1, D38.3 (common), J50.1, R126.2; also elsewhere on the board

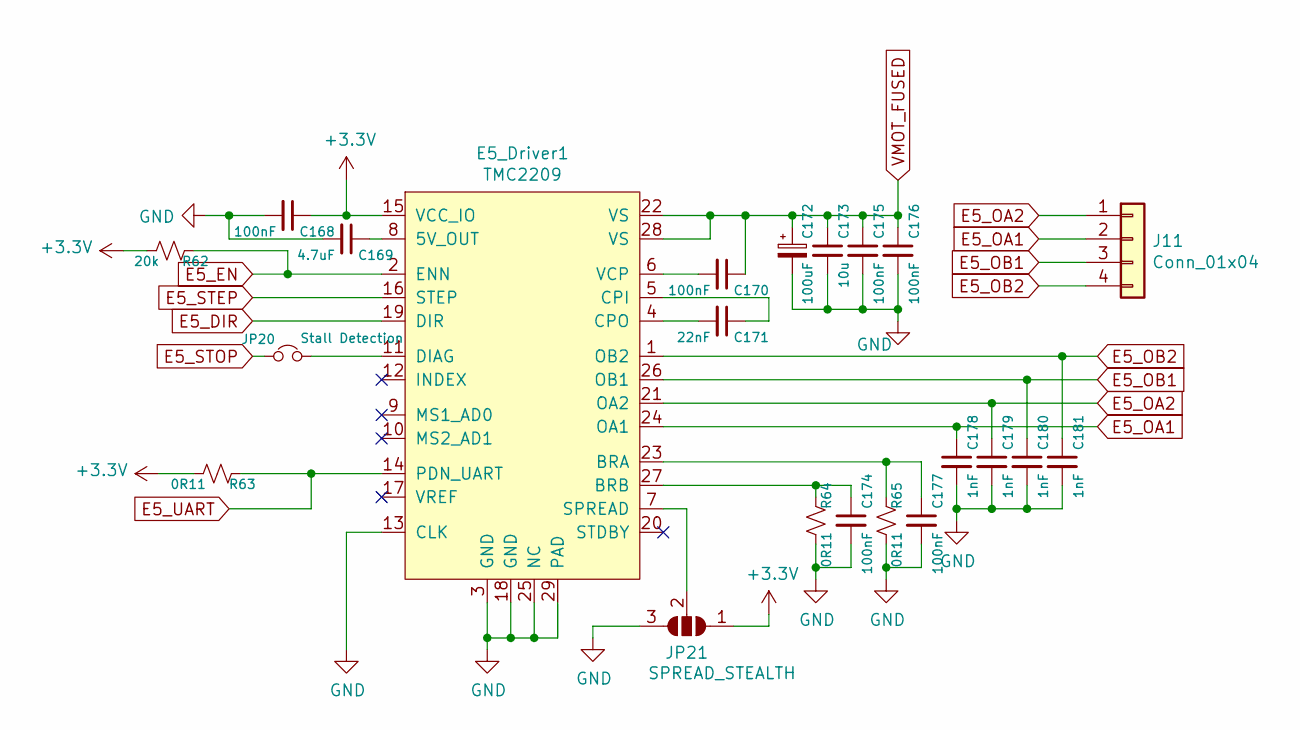
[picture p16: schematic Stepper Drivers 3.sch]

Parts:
C168, C170, C174, C175, C176, C177: 100nF; C_0603_1608Metric_Pad1.05x0.95mm_HandSolder
C169: 4.7uF; C_0805_2012Metric_Pad1.15x1.40mm_HandSolder
C171: 22nF; C_0603_1608Metric_Pad1.05x0.95mm_HandSolder
C172: 100uF; CP_Elec_6.3x7.7
C173: 10u; C_0805_2012Metric_Pad1.15x1.40mm_HandSolder
C178, C179, C180, C181: 1nF; C_0603_1608Metric_Pad1.05x0.95mm_HandSolder
E5_Driver1: TMC2209; QFN-28-1EP_5x5mm_P0.5mm_EP3.35x3.35mm_ThermalVias
J11: Conn_01x04; Molex_KK-254_AE-6410-04A_1x04_P2.54mm_Vertical
JP20: Stall Detection; PinHeader_1x02_P2.54mm_Vertical
JP21: SPREAD_STEALTH; SolderJumper-3_P1.3mm_Open_RoundedPad1.0x1.5mm
R62: 20k; R_0603_1608Metric_Pad1.05x0.95mm_HandSolder
R63, R64, R65: 0R11; R_0805_2012Metric_Pad1.15x1.40mm_HandSolder

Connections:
+3V3: C168.1, E5_Driver1.15 (VCC_IO), JP21.1 (A), R62.2, R63.2; also elsewhere on the board
E5_DIR: E5_Driver1.19 (DIR); also elsewhere on the board
E5_EN: E5_Driver1.2 (ENN), R62.1; also elsewhere on the board
E5_OA1: C178.1, E5_Driver1.24 (OA1), J11.2
E5_OA2: C179.1, E5_Driver1.21 (OA2), J11.1
E5_OB1: C180.1, E5_Driver1.26 (OB1), J11.3
E5_OB2: C181.1, E5_Driver1.1 (OB2), J11.4
E5_STEP: E5_Driver1.16 (STEP); also elsewhere on the board
E5_STOP: JP20.1; also elsewhere on the board
E5_UART: E5_Driver1.14 (PDN_UART), R63.1; also elsewhere on the board
GND: C168.2, C169.2, C172.2, C173.2, C174.2, C175.2, C176.2, C177.2, C178.2, C179.2, C180.2, C181.2, E5_Driver1.3 (GND), E5_Driver1.13 (CLK), E5_Driver1.18 (GND), E5_Driver1.25 (NC), E5_Driver1.29 (PAD), JP21.3 (B), R64.2, R65.2; also elsewhere on the board
unnamed: C169.1, E5_Driver1.8 (5V_OUT)
unnamed: C170.2, E5_Driver1.6 (VCP)
unnamed: C171.1, E5_Driver1.5 (CPI)
unnamed: C171.2, E5_Driver1.4 (CPO)
unnamed: C174.1, E5_Driver1.27 (BRB), R64.1
unnamed: C177.1, E5_Driver1.23 (BRA), R65.1
unnamed: E5_Driver1.7 (SPREAD), JP21.2 (C)
unnamed: E5_Driver1.11 (DIAG), JP20.2
VMOT_FUSED: C170.1, C172.1, C173.1, C175.1, C176.1, E5_Driver1.22 (VS), E5_Driver1.28 (VS); also elsewhere on the board

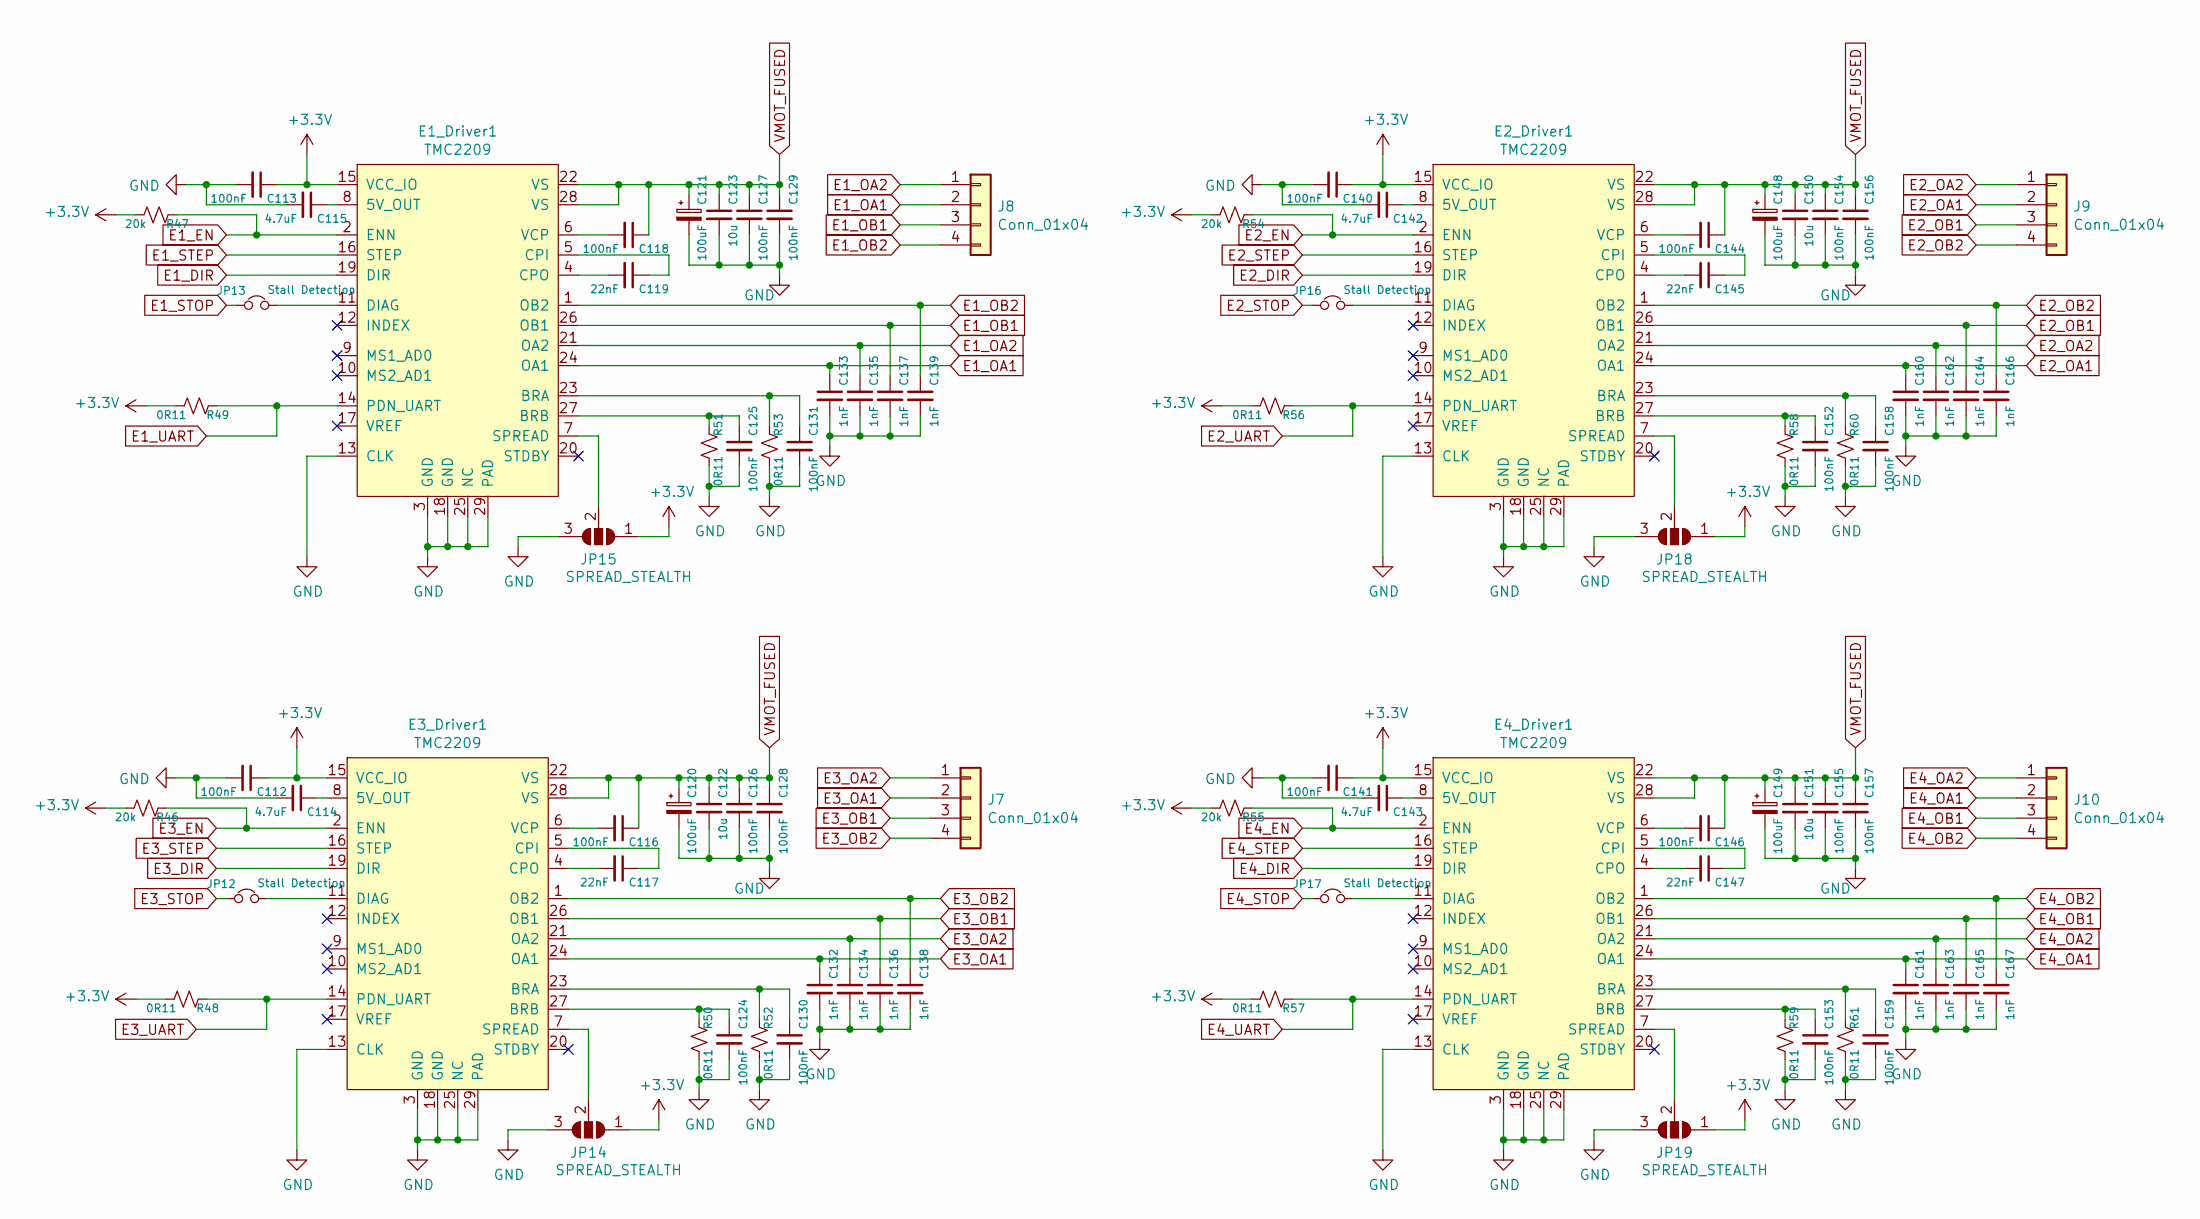
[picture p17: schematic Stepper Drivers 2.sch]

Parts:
C112, C113, C116, C118, C124, C125, C126, C127, C128, C129, C130, C131, C140, C141, C144, C146, C152, C153, C154, C155, C156, C157, C158, C159: 100nF; C_0603_1608Metric_Pad1.05x0.95mm_HandSolder
C114, C115, C142, C143: 4.7uF; C_0805_2012Metric_Pad1.15x1.40mm_HandSolder
C117, C119, C145, C147: 22nF; C_0603_1608Metric_Pad1.05x0.95mm_HandSolder
C120, C121, C148, C149: 100uF; CP_Elec_6.3x7.7
C122, C123, C150, C151: 10u; C_0805_2012Metric_Pad1.15x1.40mm_HandSolder
C132, C133, C134, C135, C136, C137, C138, C139, C160, C161, C162, C163, C164, C165, C166, C167: 1nF; C_0603_1608Metric_Pad1.05x0.95mm_HandSolder
E1_Driver1, E2_Driver1, E3_Driver1, E4_Driver1: TMC2209; QFN-28-1EP_5x5mm_P0.5mm_EP3.35x3.35mm_ThermalVias
J7, J8, J9, J10: Conn_01x04; Molex_KK-254_AE-6410-04A_1x04_P2.54mm_Vertical
JP12, JP13, JP16, JP17: Stall Detection; PinHeader_1x02_P2.54mm_Vertical
JP14, JP15, JP18, JP19: SPREAD_STEALTH; SolderJumper-3_P1.3mm_Open_RoundedPad1.0x1.5mm
R46, R47, R54, R55: 20k; R_0603_1608Metric_Pad1.05x0.95mm_HandSolder
R48, R49, R50, R51, R52, R53, R56, R57, R58, R59, R60, R61: 0R11; R_0805_2012Metric_Pad1.15x1.40mm_HandSolder

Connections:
+3V3: C112.1, C113.1, C140.1, C141.1, E1_Driver1.15 (VCC_IO), E2_Driver1.15 (VCC_IO), E3_Driver1.15 (VCC_IO), E4_Driver1.15 (VCC_IO), JP14.1 (A), JP15.1 (A), JP18.1 (A), JP19.1 (A), R46.2, R47.2, R48.2, R49.2, R54.2, R55.2, R56.2, R57.2; also elsewhere on the board
E1_DIR: E1_Driver1.19 (DIR); also elsewhere on the board
E1_EN: E1_Driver1.2 (ENN), R47.1; also elsewhere on the board
E1_OA1: C133.1, E1_Driver1.24 (OA1), J8.2
E1_OA2: C135.1, E1_Driver1.21 (OA2), J8.1
E1_OB1: C137.1, E1_Driver1.26 (OB1), J8.3
E1_OB2: C139.1, E1_Driver1.1 (OB2), J8.4
E1_STEP: E1_Driver1.16 (STEP); also elsewhere on the board
E1_STOP: JP13.1; also elsewhere on the board
E1_UART: E1_Driver1.14 (PDN_UART), R49.1; also elsewhere on the board
E2_DIR: E2_Driver1.19 (DIR); also elsewhere on the board
E2_EN: E2_Driver1.2 (ENN), R54.1; also elsewhere on the board
E2_OA1: C160.1, E2_Driver1.24 (OA1), J9.2
E2_OA2: C162.1, E2_Driver1.21 (OA2), J9.1
E2_OB1: C164.1, E2_Driver1.26 (OB1), J9.3
E2_OB2: C166.1, E2_Driver1.1 (OB2), J9.4
E2_STEP: E2_Driver1.16 (STEP); also elsewhere on the board
E2_STOP: JP16.1; also elsewhere on the board
E2_UART: E2_Driver1.14 (PDN_UART), R56.1; also elsewhere on the board
E3_DIR: E3_Driver1.19 (DIR); also elsewhere on the board
E3_EN: E3_Driver1.2 (ENN), R46.1; also elsewhere on the board
E3_OA1: C132.1, E3_Driver1.24 (OA1), J7.2
E3_OA2: C134.1, E3_Driver1.21 (OA2), J7.1
E3_OB1: C136.1, E3_Driver1.26 (OB1), J7.3
E3_OB2: C138.1, E3_Driver1.1 (OB2), J7.4
E3_STEP: E3_Driver1.16 (STEP); also elsewhere on the board
E3_STOP: JP12.1; also elsewhere on the board
E3_UART: E3_Driver1.14 (PDN_UART), R48.1; also elsewhere on the board
E4_DIR: E4_Driver1.19 (DIR); also elsewhere on the board
E4_EN: E4_Driver1.2 (ENN), R55.1; also elsewhere on the board
E4_OA1: C161.1, E4_Driver1.24 (OA1), J10.2
E4_OA2: C163.1, E4_Driver1.21 (OA2), J10.1
E4_OB1: C165.1, E4_Driver1.26 (OB1), J10.3
E4_OB2: C167.1, E4_Driver1.1 (OB2), J10.4
E4_STEP: E4_Driver1.16 (STEP); also elsewhere on the board
E4_STOP: JP17.1; also elsewhere on the board
E4_UART: E4_Driver1.14 (PDN_UART), R57.1; also elsewhere on the board
GND: C112.2, C113.2, C114.2, C115.2, C120.2, C121.2, C122.2, C123.2, C124.2, C125.2, C126.2, C127.2, C128.2, C129.2, C130.2, C131.2, C132.2, C133.2, C134.2, C135.2, C136.2, C137.2, C138.2, C139.2, C140.2, C141.2, C142.2, C143.2, C148.2, C149.2, C150.2, C151.2, C152.2, C153.2, C154.2, C155.2, C156.2, C157.2, C158.2, C159.2, C160.2, C161.2, C162.2, C163.2, C164.2, C165.2, C166.2, C167.2, E1_Driver1.3 (GND), E1_Driver1.13 (CLK), E1_Driver1.18 (GND), E1_Driver1.25 (NC), E1_Driver1.29 (PAD), E2_Driver1.3 (GND), E2_Driver1.13 (CLK), E2_Driver1.18 (GND), E2_Driver1.25 (NC), E2_Driver1.29 (PAD), E3_Driver1.3 (GND), E3_Driver1.13 (CLK), E3_Driver1.18 (GND), E3_Driver1.25 (NC), E3_Driver1.29 (PAD), E4_Driver1.3 (GND), E4_Driver1.13 (CLK), E4_Driver1.18 (GND), E4_Driver1.25 (NC), E4_Driver1.29 (PAD), JP14.3 (B), JP15.3 (B), JP18.3 (B), JP19.3 (B), R50.2, R51.2, R52.2, R53.2, R58.2, R59.2, R60.2, R61.2; also elsewhere on the board
unnamed: C114.1, E3_Driver1.8 (5V_OUT)
unnamed: C115.1, E1_Driver1.8 (5V_OUT)
unnamed: C116.2, E3_Driver1.6 (VCP)
unnamed: C117.1, E3_Driver1.5 (CPI)
unnamed: C117.2, E3_Driver1.4 (CPO)
unnamed: C118.2, E1_Driver1.6 (VCP)
unnamed: C119.1, E1_Driver1.5 (CPI)
unnamed: C119.2, E1_Driver1.4 (CPO)
unnamed: C124.1, E3_Driver1.27 (BRB), R50.1
unnamed: C125.1, E1_Driver1.27 (BRB), R51.1
unnamed: C130.1, E3_Driver1.23 (BRA), R52.1
unnamed: C131.1, E1_Driver1.23 (BRA), R53.1
unnamed: C142.1, E2_Driver1.8 (5V_OUT)
unnamed: C143.1, E4_Driver1.8 (5V_OUT)
unnamed: C144.2, E2_Driver1.6 (VCP)
unnamed: C145.1, E2_Driver1.5 (CPI)
unnamed: C145.2, E2_Driver1.4 (CPO)
unnamed: C146.2, E4_Driver1.6 (VCP)
unnamed: C147.1, E4_Driver1.5 (CPI)
unnamed: C147.2, E4_Driver1.4 (CPO)
unnamed: C152.1, E2_Driver1.27 (BRB), R58.1
unnamed: C153.1, E4_Driver1.27 (BRB), R59.1
unnamed: C158.1, E2_Driver1.23 (BRA), R60.1
unnamed: C159.1, E4_Driver1.23 (BRA), R61.1
unnamed: E1_Driver1.7 (SPREAD), JP15.2 (C)
unnamed: E1_Driver1.11 (DIAG), JP13.2
unnamed: E2_Driver1.7 (SPREAD), JP18.2 (C)
unnamed: E2_Driver1.11 (DIAG), JP16.2
unnamed: E3_Driver1.7 (SPREAD), JP14.2 (C)
unnamed: E3_Driver1.11 (DIAG), JP12.2
unnamed: E4_Driver1.7 (SPREAD), JP19.2 (C)
unnamed: E4_Driver1.11 (DIAG), JP17.2
VMOT_FUSED: C116.1, C118.1, C120.1, C121.1, C122.1, C123.1, C126.1, C127.1, C128.1, C129.1, C144.1, C146.1, C148.1, C149.1, C150.1, C151.1, C154.1, C155.1, C156.1, C157.1, E1_Driver1.22 (VS), E1_Driver1.28 (VS), E2_Driver1.22 (VS), E2_Driver1.28 (VS), E3_Driver1.22 (VS), E3_Driver1.28 (VS), E4_Driver1.22 (VS), E4_Driver1.28 (VS); also elsewhere on the board

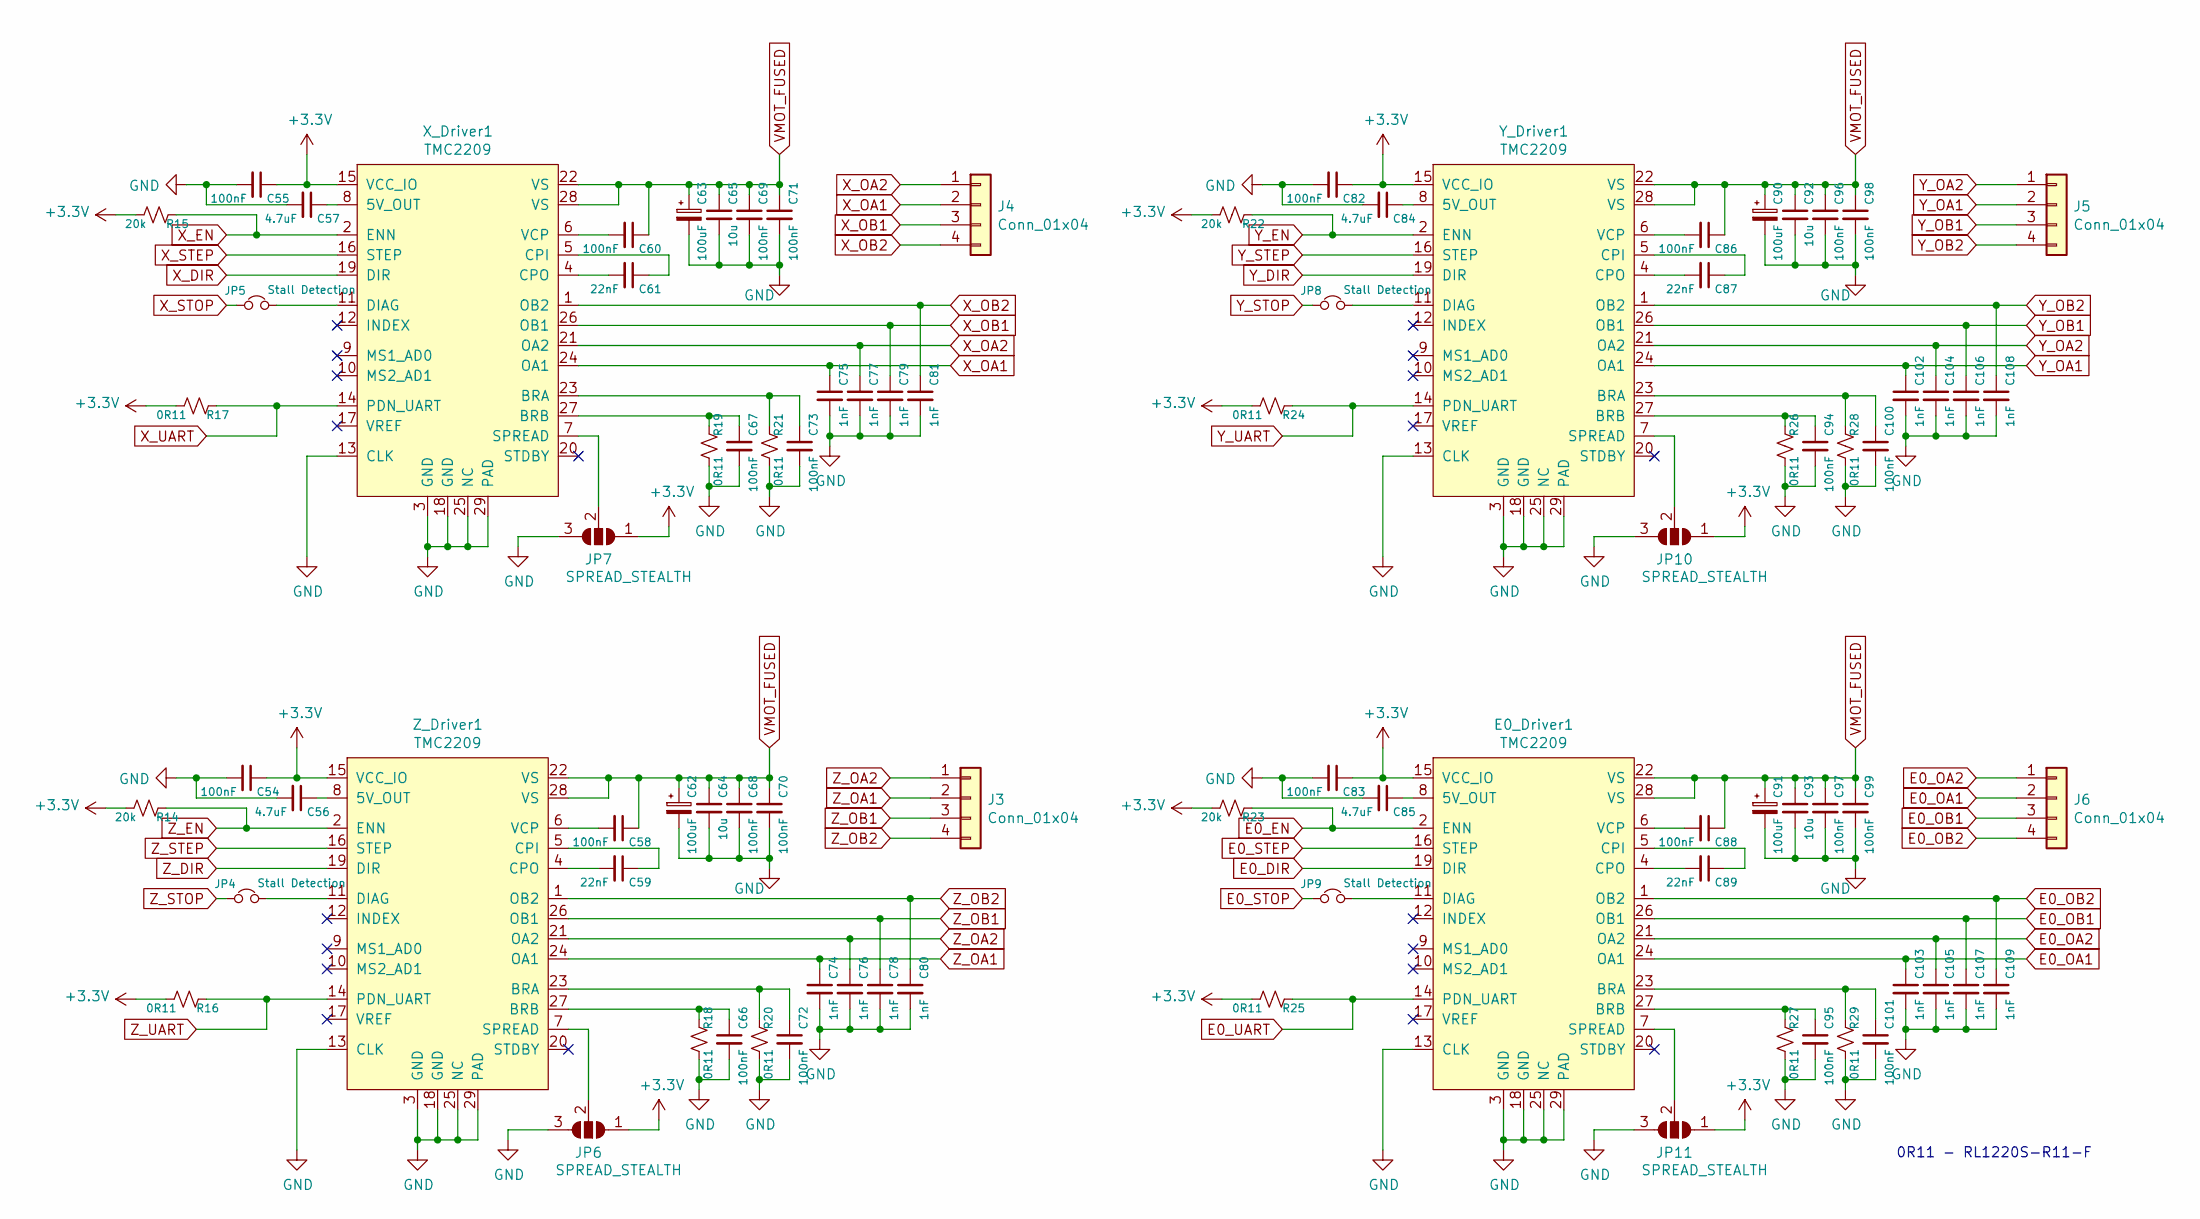
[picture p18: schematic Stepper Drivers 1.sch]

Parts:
C54, C55, C58, C60, C66, C67, C68, C69, C70, C71, C72, C73, C82, C83, C86, C88, C94, C95, C96, C97, C98, C99, C100, C101: 100nF; C_0603_1608Metric_Pad1.05x0.95mm_HandSolder
C56, C57, C84, C85: 4.7uF; C_0805_2012Metric_Pad1.15x1.40mm_HandSolder
C59, C61, C87, C89: 22nF; C_0603_1608Metric_Pad1.05x0.95mm_HandSolder
C62, C63, C90, C91: 100uF; CP_Elec_6.3x7.7
C64, C65, C92, C93: 10u; C_0805_2012Metric_Pad1.15x1.40mm_HandSolder
C74, C75, C76, C77, C78, C79, C80, C81, C102, C103, C104, C105, C106, C107, C108, C109: 1nF; C_0603_1608Metric_Pad1.05x0.95mm_HandSolder
E0_Driver1: TMC2209; QFN-28-1EP_5x5mm_P0.5mm_EP3.35x3.35mm_ThermalVias
J3, J4, J5, J6: Conn_01x04; Molex_KK-254_AE-6410-04A_1x04_P2.54mm_Vertical
JP4, JP5, JP8, JP9: Stall Detection; PinHeader_1x02_P2.54mm_Vertical
JP6, JP7, JP10, JP11: SPREAD_STEALTH; SolderJumper-3_P1.3mm_Open_RoundedPad1.0x1.5mm
R14, R15, R22, R23: 20k; R_0603_1608Metric_Pad1.05x0.95mm_HandSolder
R16, R17, R18, R19, R20, R21, R24, R25, R26, R27, R28, R29: 0R11; R_0805_2012Metric_Pad1.15x1.40mm_HandSolder
X_Driver1: TMC2209; QFN-28-1EP_5x5mm_P0.5mm_EP3.35x3.35mm_ThermalVias
Y_Driver1: TMC2209; QFN-28-1EP_5x5mm_P0.5mm_EP3.35x3.35mm_ThermalVias
Z_Driver1: TMC2209; QFN-28-1EP_5x5mm_P0.5mm_EP3.35x3.35mm_ThermalVias

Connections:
+3V3: C54.1, C55.1, C82.1, C83.1, E0_Driver1.15 (VCC_IO), JP6.1 (A), JP7.1 (A), JP10.1 (A), JP11.1 (A), R14.2, R15.2, R16.2, R17.2, R22.2, R23.2, R24.2, R25.2, X_Driver1.15 (VCC_IO), Y_Driver1.15 (VCC_IO), Z_Driver1.15 (VCC_IO); also elsewhere on the board
E0_DIR: E0_Driver1.19 (DIR); also elsewhere on the board
E0_EN: E0_Driver1.2 (ENN), R23.1; also elsewhere on the board
E0_OA1: C103.1, E0_Driver1.24 (OA1), J6.2
E0_OA2: C105.1, E0_Driver1.21 (OA2), J6.1
E0_OB1: C107.1, E0_Driver1.26 (OB1), J6.3
E0_OB2: C109.1, E0_Driver1.1 (OB2), J6.4
E0_STEP: E0_Driver1.16 (STEP); also elsewhere on the board
E0_STOP: JP9.1; also elsewhere on the board
E0_UART: E0_Driver1.14 (PDN_UART), R25.1; also elsewhere on the board
GND: C54.2, C55.2, C56.2, C57.2, C62.2, C63.2, C64.2, C65.2, C66.2, C67.2, C68.2, C69.2, C70.2, C71.2, C72.2, C73.2, C74.2, C75.2, C76.2, C77.2, C78.2, C79.2, C80.2, C81.2, C82.2, C83.2, C84.2, C85.2, C90.2, C91.2, C92.2, C93.2, C94.2, C95.2, C96.2, C97.2, C98.2, C99.2, C100.2, C101.2, C102.2, C103.2, C104.2, C105.2, C106.2, C107.2, C108.2, C109.2, E0_Driver1.3 (GND), E0_Driver1.13 (CLK), E0_Driver1.18 (GND), E0_Driver1.25 (NC), E0_Driver1.29 (PAD), JP6.3 (B), JP7.3 (B), JP10.3 (B), JP11.3 (B), R18.2, R19.2, R20.2, R21.2, R26.2, R27.2, R28.2, R29.2, X_Driver1.3 (GND), X_Driver1.13 (CLK), X_Driver1.18 (GND), X_Driver1.25 (NC), X_Driver1.29 (PAD), Y_Driver1.3 (GND), Y_Driver1.13 (CLK), Y_Driver1.18 (GND), Y_Driver1.25 (NC), Y_Driver1.29 (PAD), Z_Driver1.3 (GND), Z_Driver1.13 (CLK), Z_Driver1.18 (GND), Z_Driver1.25 (NC), Z_Driver1.29 (PAD); also elsewhere on the board
unnamed: C56.1, Z_Driver1.8 (5V_OUT)
unnamed: C57.1, X_Driver1.8 (5V_OUT)
unnamed: C58.2, Z_Driver1.6 (VCP)
unnamed: C59.1, Z_Driver1.5 (CPI)
unnamed: C59.2, Z_Driver1.4 (CPO)
unnamed: C60.2, X_Driver1.6 (VCP)
unnamed: C61.1, X_Driver1.5 (CPI)
unnamed: C61.2, X_Driver1.4 (CPO)
unnamed: C66.1, R18.1, Z_Driver1.27 (BRB)
unnamed: C67.1, R19.1, X_Driver1.27 (BRB)
unnamed: C72.1, R20.1, Z_Driver1.23 (BRA)
unnamed: C73.1, R21.1, X_Driver1.23 (BRA)
unnamed: C84.1, Y_Driver1.8 (5V_OUT)
unnamed: C85.1, E0_Driver1.8 (5V_OUT)
unnamed: C86.2, Y_Driver1.6 (VCP)
unnamed: C87.1, Y_Driver1.5 (CPI)
unnamed: C87.2, Y_Driver1.4 (CPO)
unnamed: C88.2, E0_Driver1.6 (VCP)
unnamed: C89.1, E0_Driver1.5 (CPI)
unnamed: C89.2, E0_Driver1.4 (CPO)
unnamed: C94.1, R26.1, Y_Driver1.27 (BRB)
unnamed: C95.1, E0_Driver1.27 (BRB), R27.1
unnamed: C100.1, R28.1, Y_Driver1.23 (BRA)
unnamed: C101.1, E0_Driver1.23 (BRA), R29.1
unnamed: E0_Driver1.7 (SPREAD), JP11.2 (C)
unnamed: E0_Driver1.11 (DIAG), JP9.2
unnamed: JP4.2, Z_Driver1.11 (DIAG)
unnamed: JP5.2, X_Driver1.11 (DIAG)
unnamed: JP6.2 (C), Z_Driver1.7 (SPREAD)
unnamed: JP7.2 (C), X_Driver1.7 (SPREAD)
unnamed: JP8.2, Y_Driver1.11 (DIAG)
unnamed: JP10.2 (C), Y_Driver1.7 (SPREAD)
VMOT_FUSED: C58.1, C60.1, C62.1, C63.1, C64.1, C65.1, C68.1, C69.1, C70.1, C71.1, C86.1, C88.1, C90.1, C91.1, C92.1, C93.1, C96.1, C97.1, C98.1, C99.1, E0_Driver1.22 (VS), E0_Driver1.28 (VS), X_Driver1.22 (VS), X_Driver1.28 (VS), Y_Driver1.22 (VS), Y_Driver1.28 (VS), Z_Driver1.22 (VS), Z_Driver1.28 (VS); also elsewhere on the board
X_DIR: X_Driver1.19 (DIR); also elsewhere on the board
X_EN: R15.1, X_Driver1.2 (ENN); also elsewhere on the board
X_OA1: C75.1, J4.2, X_Driver1.24 (OA1)
X_OA2: C77.1, J4.1, X_Driver1.21 (OA2)
X_OB1: C79.1, J4.3, X_Driver1.26 (OB1)
X_OB2: C81.1, J4.4, X_Driver1.1 (OB2)
X_STEP: X_Driver1.16 (STEP); also elsewhere on the board
X_STOP: JP5.1; also elsewhere on the board
X_UART: R17.1, X_Driver1.14 (PDN_UART); also elsewhere on the board
Y_DIR: Y_Driver1.19 (DIR); also elsewhere on the board
Y_EN: R22.1, Y_Driver1.2 (ENN); also elsewhere on the board
Y_OA1: C102.1, J5.2, Y_Driver1.24 (OA1)
Y_OA2: C104.1, J5.1, Y_Driver1.21 (OA2)
Y_OB1: C106.1, J5.3, Y_Driver1.26 (OB1)
Y_OB2: C108.1, J5.4, Y_Driver1.1 (OB2)
Y_STEP: Y_Driver1.16 (STEP); also elsewhere on the board
Y_STOP: JP8.1; also elsewhere on the board
Y_UART: R24.1, Y_Driver1.14 (PDN_UART); also elsewhere on the board
Z_DIR: Z_Driver1.19 (DIR); also elsewhere on the board
Z_EN: R14.1, Z_Driver1.2 (ENN); also elsewhere on the board
Z_OA1: C74.1, J3.2, Z_Driver1.24 (OA1)
Z_OA2: C76.1, J3.1, Z_Driver1.21 (OA2)
Z_OB1: C78.1, J3.3, Z_Driver1.26 (OB1)
Z_OB2: C80.1, J3.4, Z_Driver1.1 (OB2)
Z_STEP: Z_Driver1.16 (STEP); also elsewhere on the board
Z_STOP: JP4.1; also elsewhere on the board
Z_UART: R16.1, Z_Driver1.14 (PDN_UART); also elsewhere on the board

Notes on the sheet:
0R11 - RL1220S-R11-F

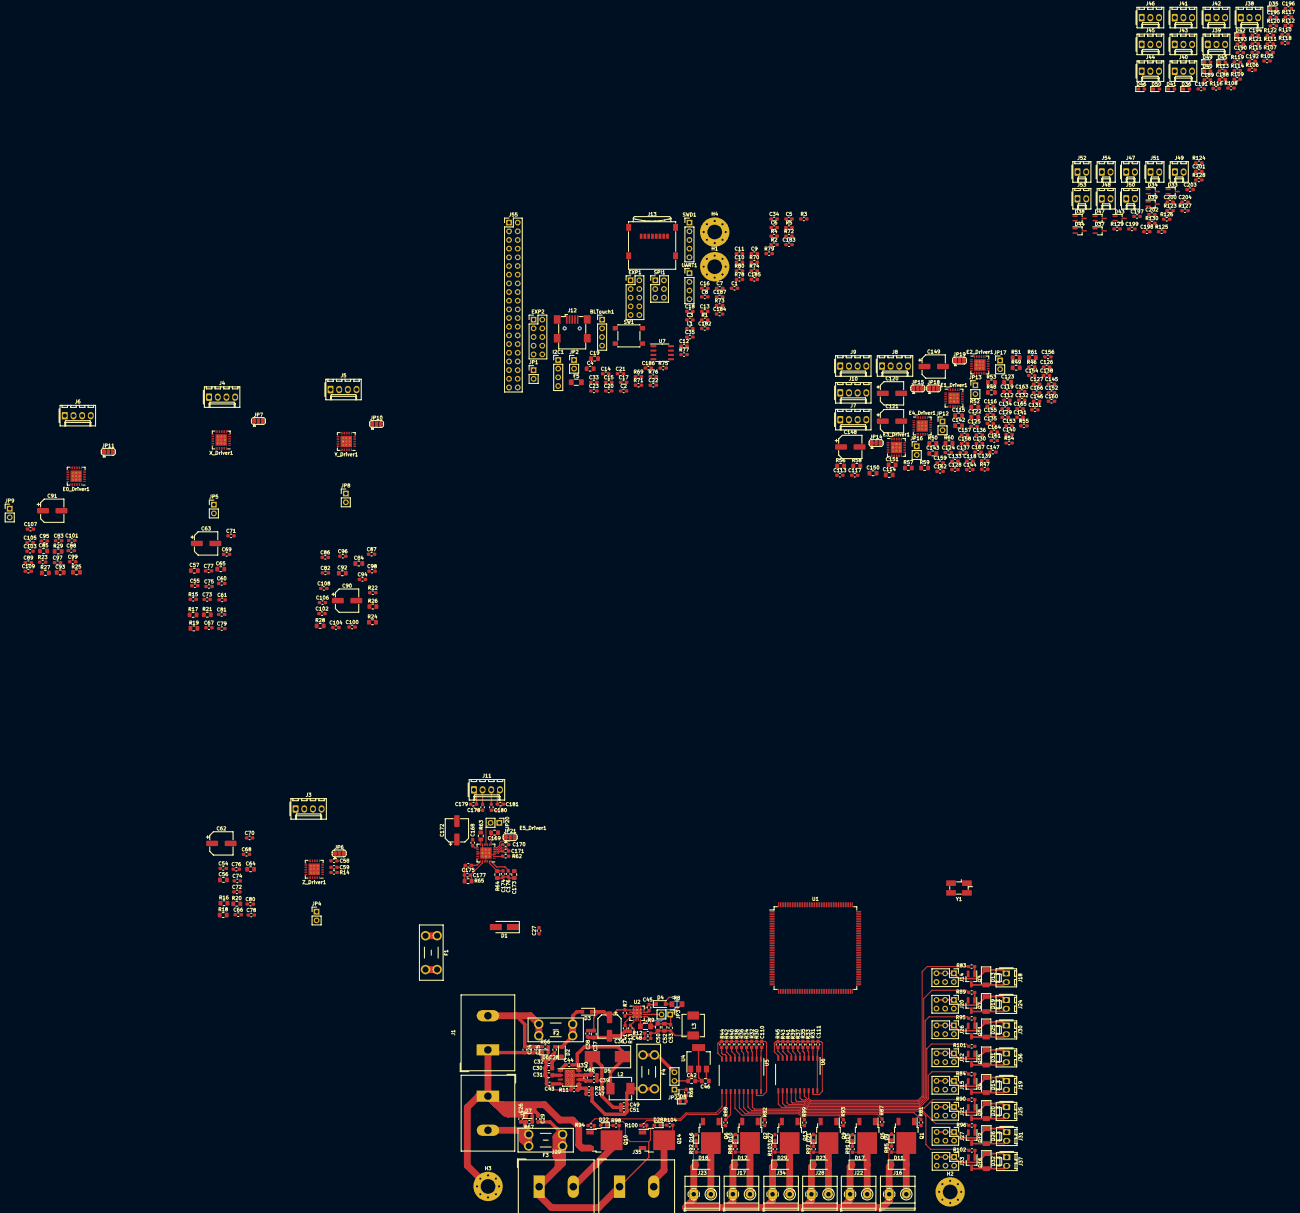
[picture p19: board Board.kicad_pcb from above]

Board: 4 copper layers, 511 parts (0 on the bottom side), 342 nets.

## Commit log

2020-10-26 Initial Commit.
    [Board.kicad_pcb, Board.sch, Endstops.sch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]
2020-10-29 added library for MOSFET Drivers
2020-10-29 Started implementing MOSFET drivers
    [Fans and Heaters.sch]
2020-10-29 added resistor numbers
    [Fans and Heaters.sch, Power.sch, Stepper Drivers 1.sch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]
2020-10-29 added MOSFETs schematic for fans and heaters.
    [Fans and Heaters.sch]
2020-10-29 added endstop schematic
    [Endstops.sch]
2020-10-29 Added thermistor schem
    [Thermistors.sch]
2020-10-29 small revisions
    [Power.sch]
2020-10-30 added USB and micro SD card
    [MCU.sch]
2020-10-30 added EEPROM and peripheral libraries
    [MCU.sch]
2020-10-30 Completed Labelling of Schematic - All nets attached
    [MCU.sch, Power.sch]
2020-10-30 added raspberry pi header
    [Endstops.sch, Fans and Heaters.sch, MCU.sch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]
2020-10-30 generated BOM
    [Board.csv]
2020-10-30 added library
    [MCU.sch]
2020-11-01 assigned some footprints
    [MCU.sch, Power.sch, Stepper Drivers 1.sch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]
2020-11-02 associated more footprints
    [Endstops.sch, Fans and Heaters.sch, MCU.sch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]
2020-11-02 Added more footprints
    [Board.sch, Endstops.sch, Fans and Heaters.sch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]
2020-11-02 finished associating footprints with symbols
    [Fans and Heaters.sch, MCU.sch, Power.sch]
2020-11-02 started initial layout
    [Fans and Heaters.sch, MCU.sch, Power.sch]
2020-11-02 Roughtly Layed out power converters and FETs
    [Board.kicad_pcb, Power.sch]
2020-11-10 started some routing
    [Board.kicad_pcb, Stepper Drivers 1.sch, Stepper Drivers 2.sch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]
2020-11-10 small component placement
    [Board.kicad_pcb]
2020-11-11 routed mosfets and buffers
    [Board.kicad_pcb]
